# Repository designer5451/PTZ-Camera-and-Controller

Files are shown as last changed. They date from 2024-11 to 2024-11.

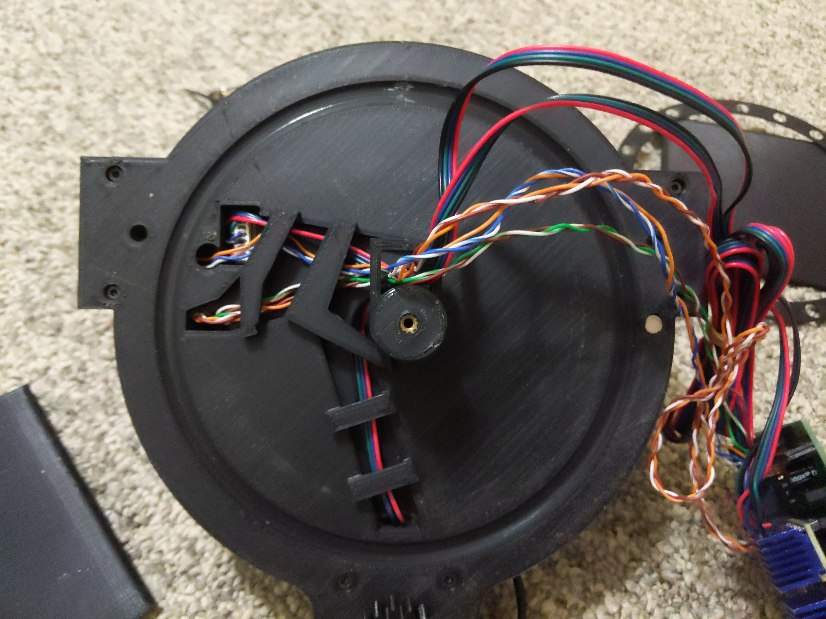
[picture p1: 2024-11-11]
Pictures/22.jpg

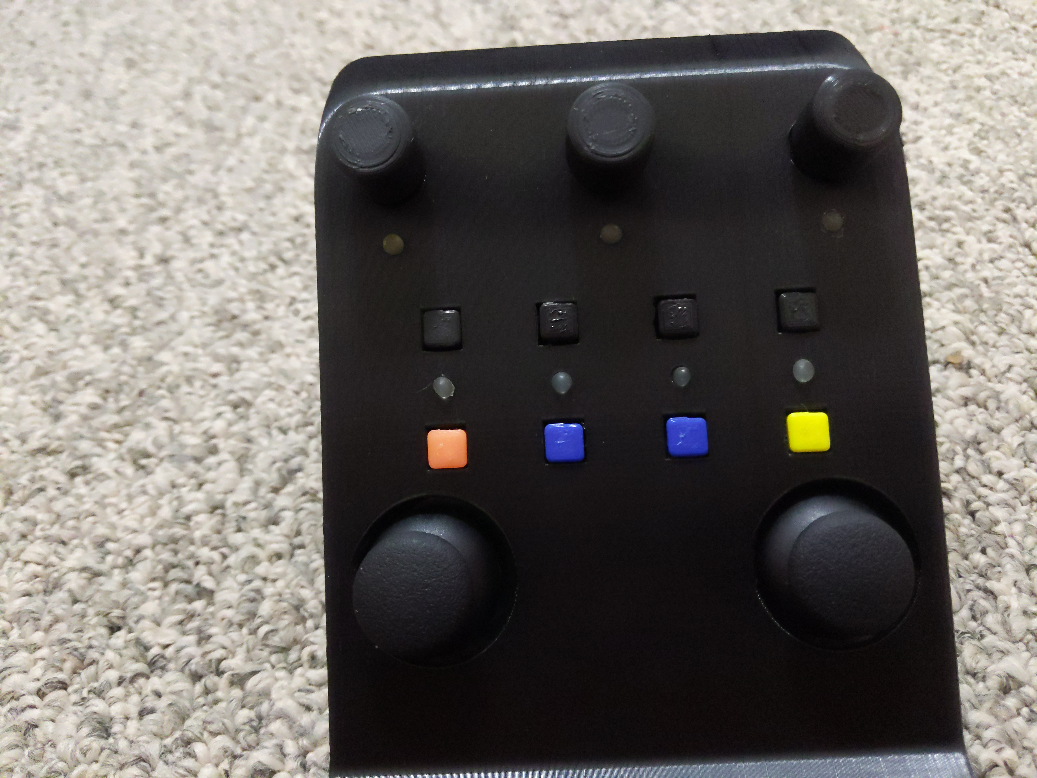
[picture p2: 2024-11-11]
Pictures/14.jpg

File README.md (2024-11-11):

This PTZ camera head uses two ESP32 microcontrollers connected via Ethernet on a standard network, communicating over a TCP connection. The controller acts as the client, while the camera head serves as the server. A PS4 controller connects to the control module via Bluetooth. The PTZ head can pan and tilt the camera and control zoom through a standard 2.5mm LANC interface.

Designed specifically for the Canon Vixia HF G30 camcorder, the PTZ head includes a servo to rotate the camera’s custom control knob. Although optimized for the Canon HF G30, it can work with other cameras that fit within its dimensions and support a standard LANC jack. However, only the Canon HF G30 can utilize the servo control for the custom knob.

The PTZ head’s PCB includes an optional slot for an extra stepper motor, which can be configured to adjust the camera lens manually if you know how to edit Fusion 360 files and the ESP32 program. The controller board program requires updates with the PTZ camera head's IP address and the PS4 controller’s Bluetooth MAC address at the beginning of the program.

To produce the two PCBs, I used JLCPCB, designing the boards in KiCad 8.0. I've attached the KiCad document, Gerber files, and a schematic screenshot. I soldered the components with a "PINECIL – Smart Mini Portable Soldering Iron (Version 2)" from [Pine64](https://pine64.com/product/pinecil-smart-mini-portable-soldering-iron/). The 3D-printed parts were designed in Fusion 360, and I’ve included the Fusion archive file along with all parts as STL files. I printed all of the 3d parts in PLA except for the to drive gears and the gear on the end of the servo which I printed in TPU.

To cushion the base of the controller, I used a hot glue gun to apply small drops, creating soft pads. I also added small glue balls  that I pushed into the controller's light holes to help diffuse the light.

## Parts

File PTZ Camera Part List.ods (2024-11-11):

PTZ
Item | Link to Item (maynot work anymore) | Estimated Price | Quantity | Total Estimated Price | Notes
USR-ES1 W5500 Ethernet Sheild | https://www.aliexpress.us/item/3256804674673261.html | $3.19 | 2 | $6.38
5 pack EC11 encoders 15 mm Half Shaft | https://www.aliexpress.us/item/2251832789732148.html | $2.86 | 1 | $2.86
5.5mm by 2.1mm Power Female Jack | https://www.aliexpress.us/item/2255799848026214.html | $1.35 | 1 | $1.35
Nema 17 42x42x22 Stepper Motor With Dupont Connector | https://www.aliexpress.us/item/3256806667671852.html | $6.07 | 2 | $12.14
10 pack 3144 Hall Effect Sensor | https://www.aliexpress.us/item/3256805950606647.html | $1.26 | 1 | $1.26
50 pack 3.3v-W3 Zener Diode Sod-323 | https://www.aliexpress.us/item/3256806999141284.html | $0.89 | 1 | $0.89
20 Pack 6mm x 2mm Neodymium Magnet | https://www.aliexpress.us/item/3256806180733507.html | $1.32 | 1 | $1.32
3A 5V Buck Converter 12mm by 17mm | https://www.aliexpress.us/item/3256806299955878.html | $0.93 | 1 | $0.93
100 pack 4.7k Resisotrs SMD | https://www.aliexpress.us/item/2251832660828415.html | $1.41 | 1 | $1.41
100 pack 5.6k Resisotrs SMD | https://www.aliexpress.us/item/2251832660828415.html | $1.02 | 1 | $1.02
100 pack 10k Resisotrs SMD | https://www.aliexpress.us/item/2251832660828415.html | $1.02 | 1 | $1.02
100 pack MMBT30094 LAM SOT-23 SMD Transistor | https://www.aliexpress.us/item/3256806841505571.html | $0.83 | 1 | $0.83
3A 12V DC Power Supply 5.5mm by 2.1mm | https://www.aliexpress.us/item/3256806788215801.html | $3.37 | 1 | $3.37
25V 100UF 6mmX7mm Aluminum electrolytic capacitor | https://www.aliexpress.us/item/3256806593044514.html | $1.45 | 1 | $1.45
TMC2209 Stepper Motor Driver | https://www.aliexpress.us/item/3256804676423170.html | $2.95 | 3 | $8.85
¼” Tripod Screw | https://www.aliexpress.us/item/3256806761503223.html | $1.36 | 1 | $1.36
38 Pin USB-C ESP32 Development Board | https://www.aliexpress.us/item/3256806034074322.html | $3.68 | 2 | $7.36
10PCS Single Row Pin Female Header Socket Pitch 2.54mm 40pin | https://www.aliexpress.us/item/2255801012106911.html | $1.82 | 1 | $1.82
10PCS Single Row Pin male Header Socket Pitch 2.54mm 40pin | https://www.aliexpress.us/item/2251832786866410.html | $2.82 | 2 | $5.64
7mm Diameter/50pcs Steel Ball | https://www.aliexpress.us/item/3256807294706153.html | $3.04 | 1 | $3.04
2 Pack PS4 Hall Effect Joystick | https://www.aliexpress.us/item/3256807040936656.html | $2.91 | 2 | $5.82 | The Yellow snap one sensor on the joysticks did not work so I had to buy twice as many as I needed and only used the black Sensors
MG995 360 degree servo | https://www.aliexpress.us/item/3256806668097478.html | $3.99 | 1 | $3.99
Bearings insides 8 mm outside 22 mm 8 Pack | https://www.aliexpress.us/item/3256807670760874.htm | $3.09 | 1 | $3.09
SMD Switches 5.2*5.2*1.5mm | https://www.aliexpress.us/item/3256804125700359.html | $0.97 | 1 | $0.97
5050 SK6812 20 Pack SMD Leds | https://www.aliexpress.us/item/3256806129701481.html | $5.00 | 1 | $5.00
SMD 10 NF capacitors 100 pack | https://www.aliexpress.us/item/2251832706484294.html | $1.81 | 1 | $1.81
M1.6 M2 M2.5 M3 M4 M5 Black Grade 12.9 Steel Hexagon Hex Socket Cap Head Screw | https://www.aliexpress.us/item/3256805018016735.html | $10.16 | 1 | $10.16
M2 M2.5 M3 M4 M5 M6 Heat Set Threaded Insert Brass Nut Hot Melt Knurled Inserts | https://www.aliexpress.us/item/3256805041162703.html | $2.79 | 1 | $2.79
Thumbstick Mushroom Cap For Sony PlayStation 4 PS4 Controlle 10 pack | https://www.aliexpress.us/item/3256807619216954.html | $1.84 | 1 | $1.84
2.5mm 3Pole Male 9 inch Cable | https://www.aliexpress.us/item/3256805153533109.html | $2.10 | 1 | $2.10
18 gauge wire for hall sensors and extending servo cord | https://www.aliexpress.us/item/3256806969799753.html | $4.43 | 1 | $4.43 | I used the wires in side ethernet riser cable
3X9X0.8 Washer 3 Needed | https://www.aliexpress.us/item/3256805615609918.html | $1.40 | 1 | $1.40
 |  |  |  | $107.70

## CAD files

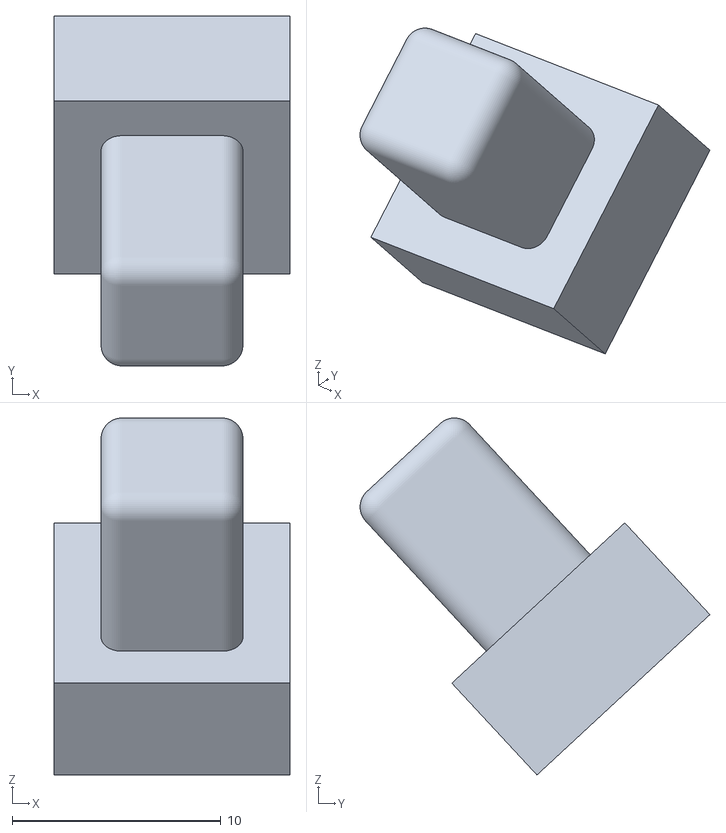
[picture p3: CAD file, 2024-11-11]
3D Files/PTZ_Camera_Controler/Button 1.stl
11.3 x 16.8 x 17.1

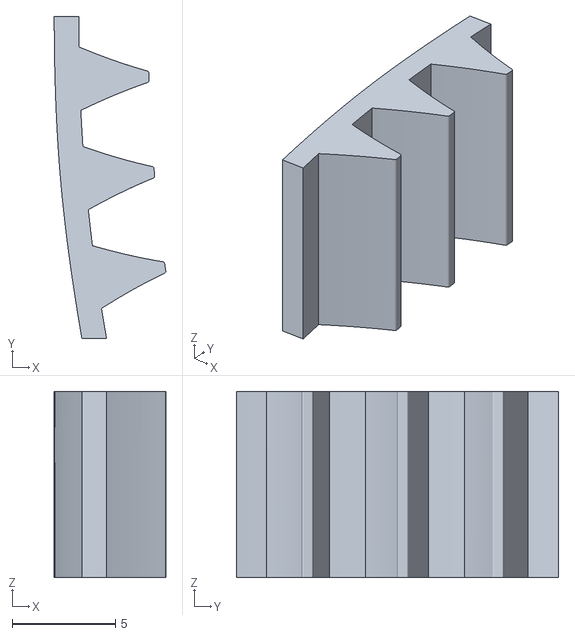
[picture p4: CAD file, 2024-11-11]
3D Files/PTZ_Camera_Head/Right Stopper.stl
5.40 x 15.6 x 9.00

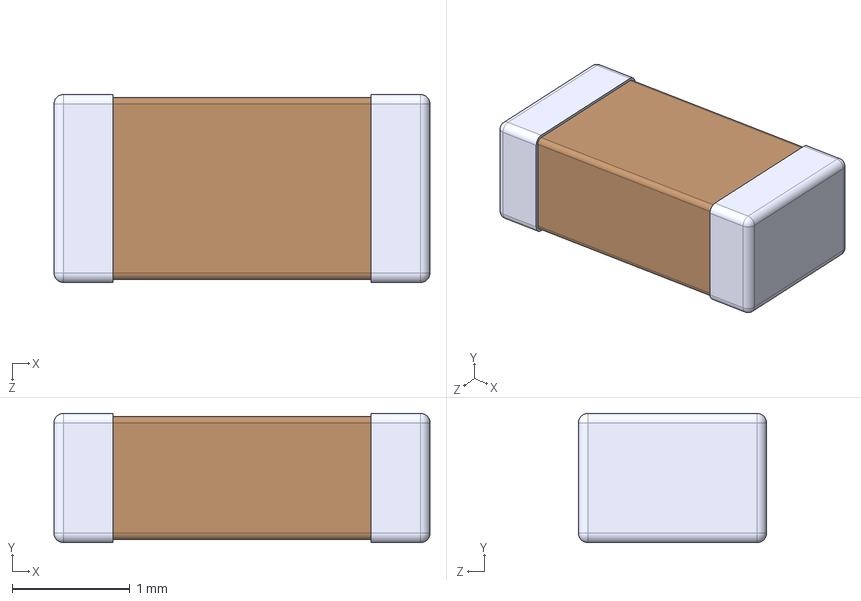
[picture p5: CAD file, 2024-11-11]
PCB Boards/PTZ_Camera_Controler V1.2/Custom Footprints/C1206C105K5RACTU_Capacitor/C1206C105K5RACTU.step
3.20 x 1.10 x 1.60 mm

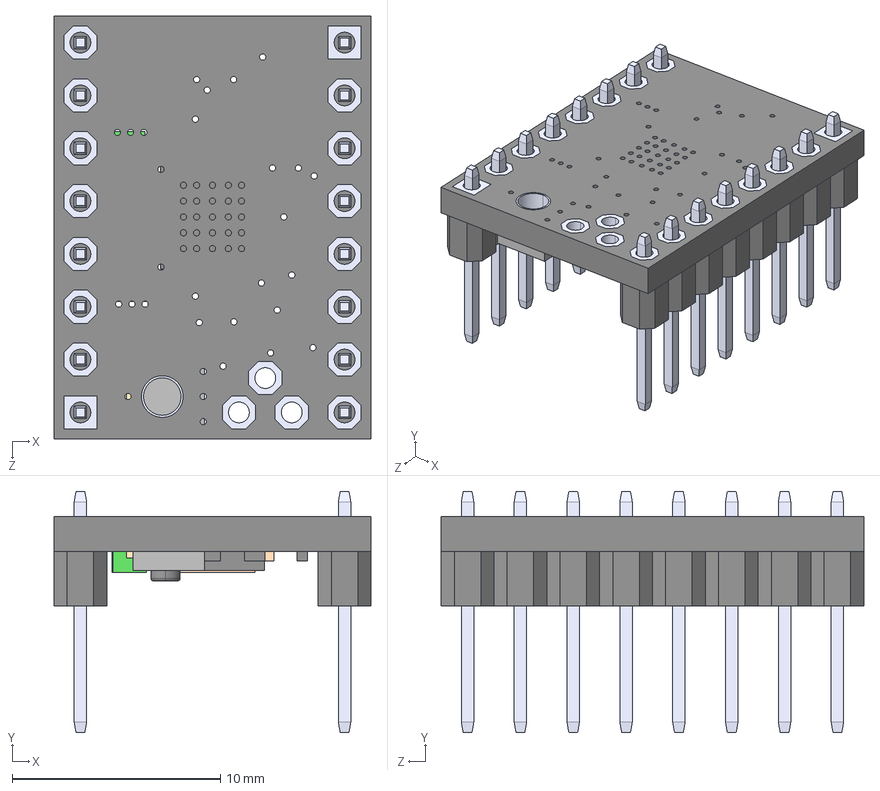
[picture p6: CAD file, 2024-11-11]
PCB Boards/PTZ_Camera_Controler V1.2/Custom Footprints/TMC2209_SILENTSTEPSTICK/TMC2209_SILENTSTEPSTICK.step
15.2 x 11.6 x 20.3 mm

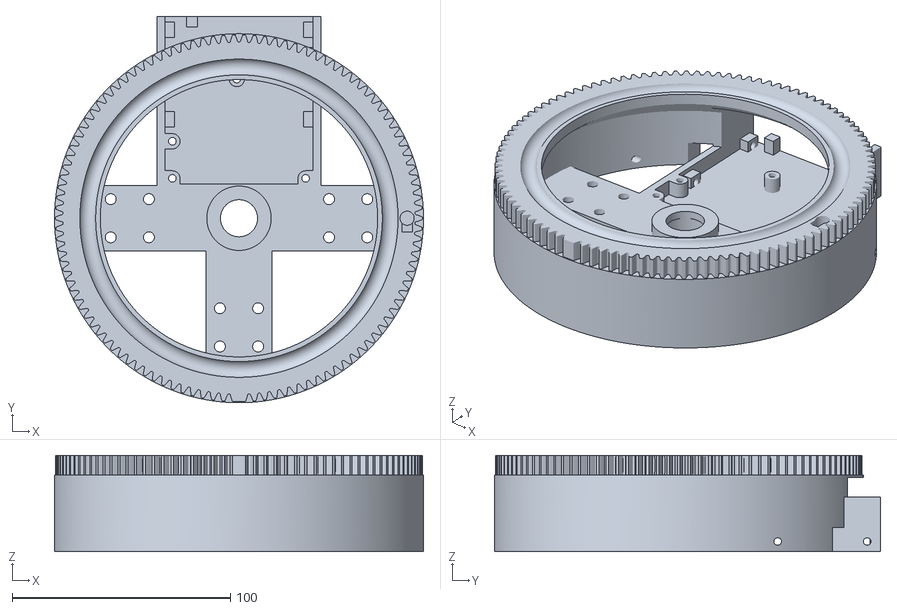
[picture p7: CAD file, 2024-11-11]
3D Files/PTZ_Camera_Head/Base.stl
169.0 x 177.0 x 44.0

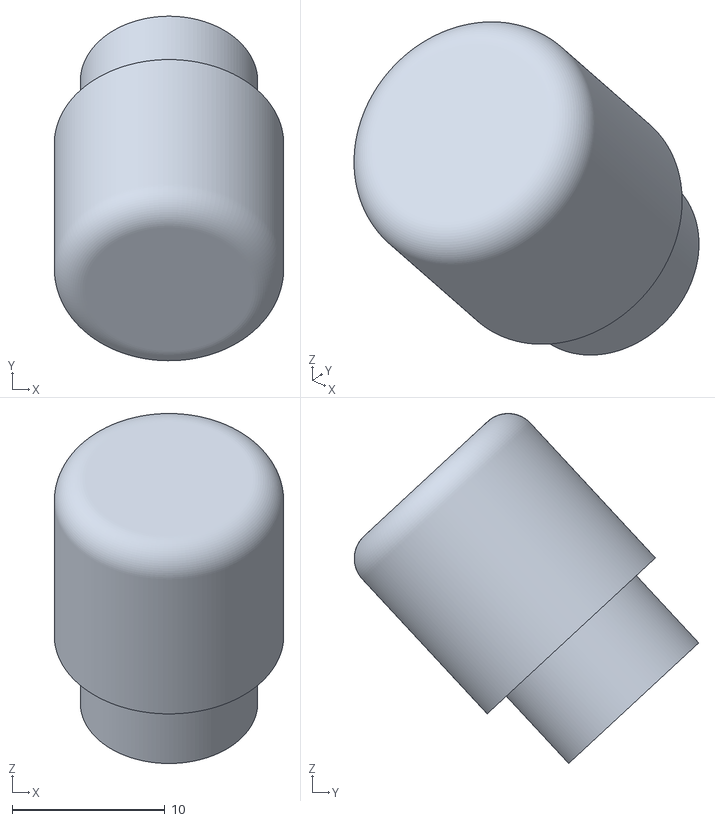
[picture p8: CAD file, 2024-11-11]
3D Files/PTZ_Camera_Controler/Knob 2.stl
15.0 x 22.5 x 22.9

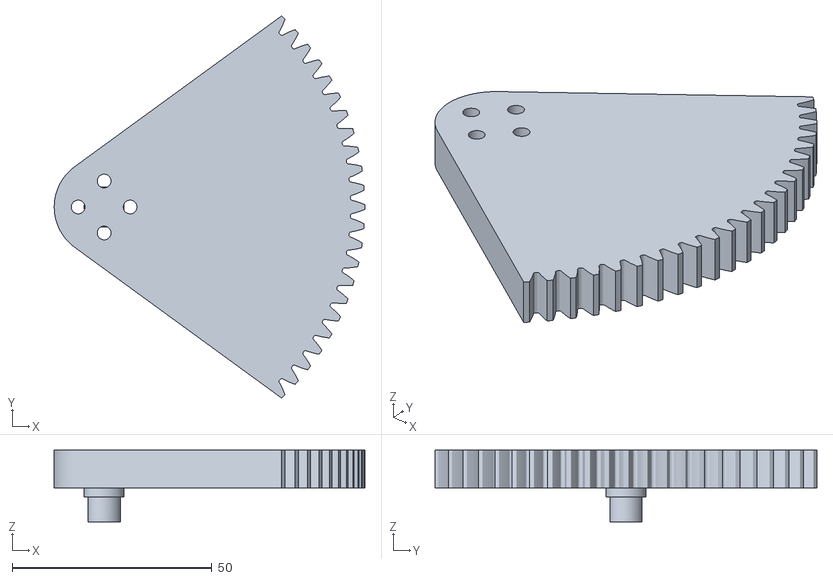
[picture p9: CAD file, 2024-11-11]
3D Files/PTZ_Camera_Head/Spur Gear (85 teeth).stl
77.7 x 95.6 x 18.0

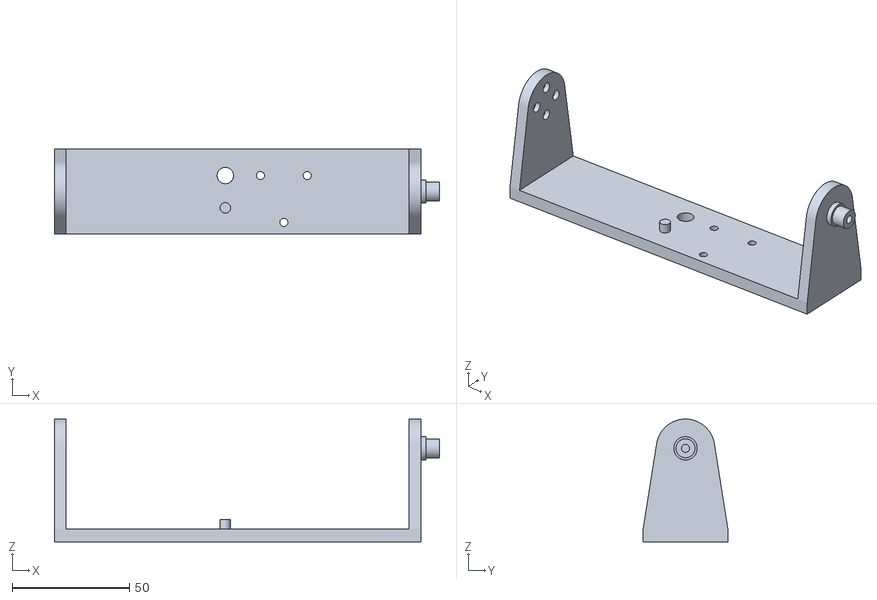
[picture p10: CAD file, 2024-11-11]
3D Files/PTZ_Camera_Head/Camera Holder.stl
164.5 x 36.3 x 52.5

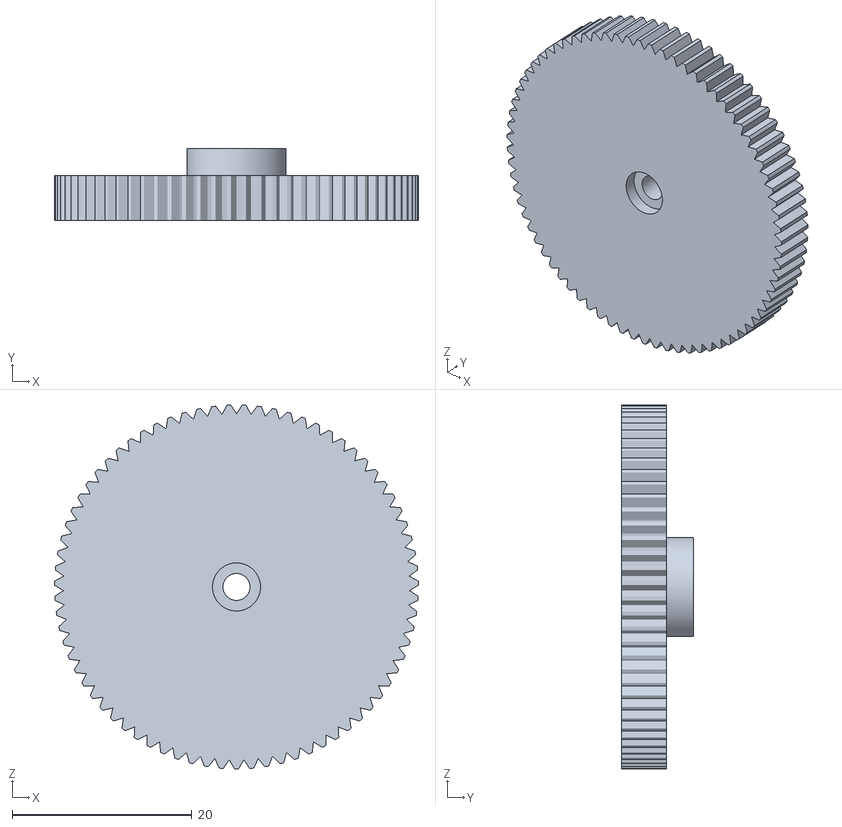
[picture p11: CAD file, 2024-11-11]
3D Files/PTZ_Camera_Head/Wheel for Servo.stl
40.5 x 8.00 x 40.5

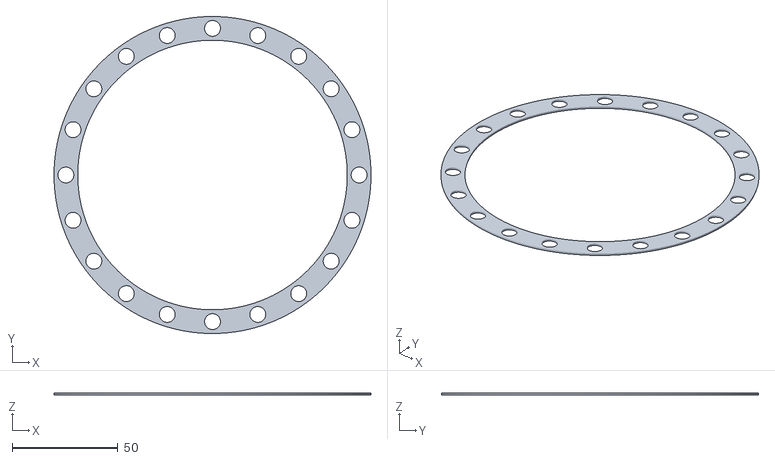
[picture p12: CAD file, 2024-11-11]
3D Files/PTZ_Camera_Head/Bearing Spacer.stl
149.7 x 149.7 x 1.00

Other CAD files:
3D Files/PTZ_Camera_Head/Left Stopper.stl
3D Files/PTZ_Camera_Controler/Back Bottom Plate.stl
3D Files/PTZ_Camera_Controler/Back Plate.stl
3D Files/PTZ_Camera_Controler/Base.stl
3D Files/PTZ_Camera_Controler/Controler+for+PTZ+Camera.f3d
3D Files/PTZ_Camera_Head/Cable Holder.stl
3D Files/PTZ_Camera_Head/Left Side Arm.stl
3D Files/PTZ_Camera_Head/Right Side Arm.stl
3D Files/PTZ_Camera_Head/Servo Holder.stl
3D Files/PTZ_Camera_Head/Spur Gear (14 teeth) (1).stl
3D Files/PTZ_Camera_Head/Spur Gear (14 teeth).stl
3D Files/PTZ_Camera_Head/Top.stl
3D Files/PTZ_Camera_Head/Wall Mount.stl

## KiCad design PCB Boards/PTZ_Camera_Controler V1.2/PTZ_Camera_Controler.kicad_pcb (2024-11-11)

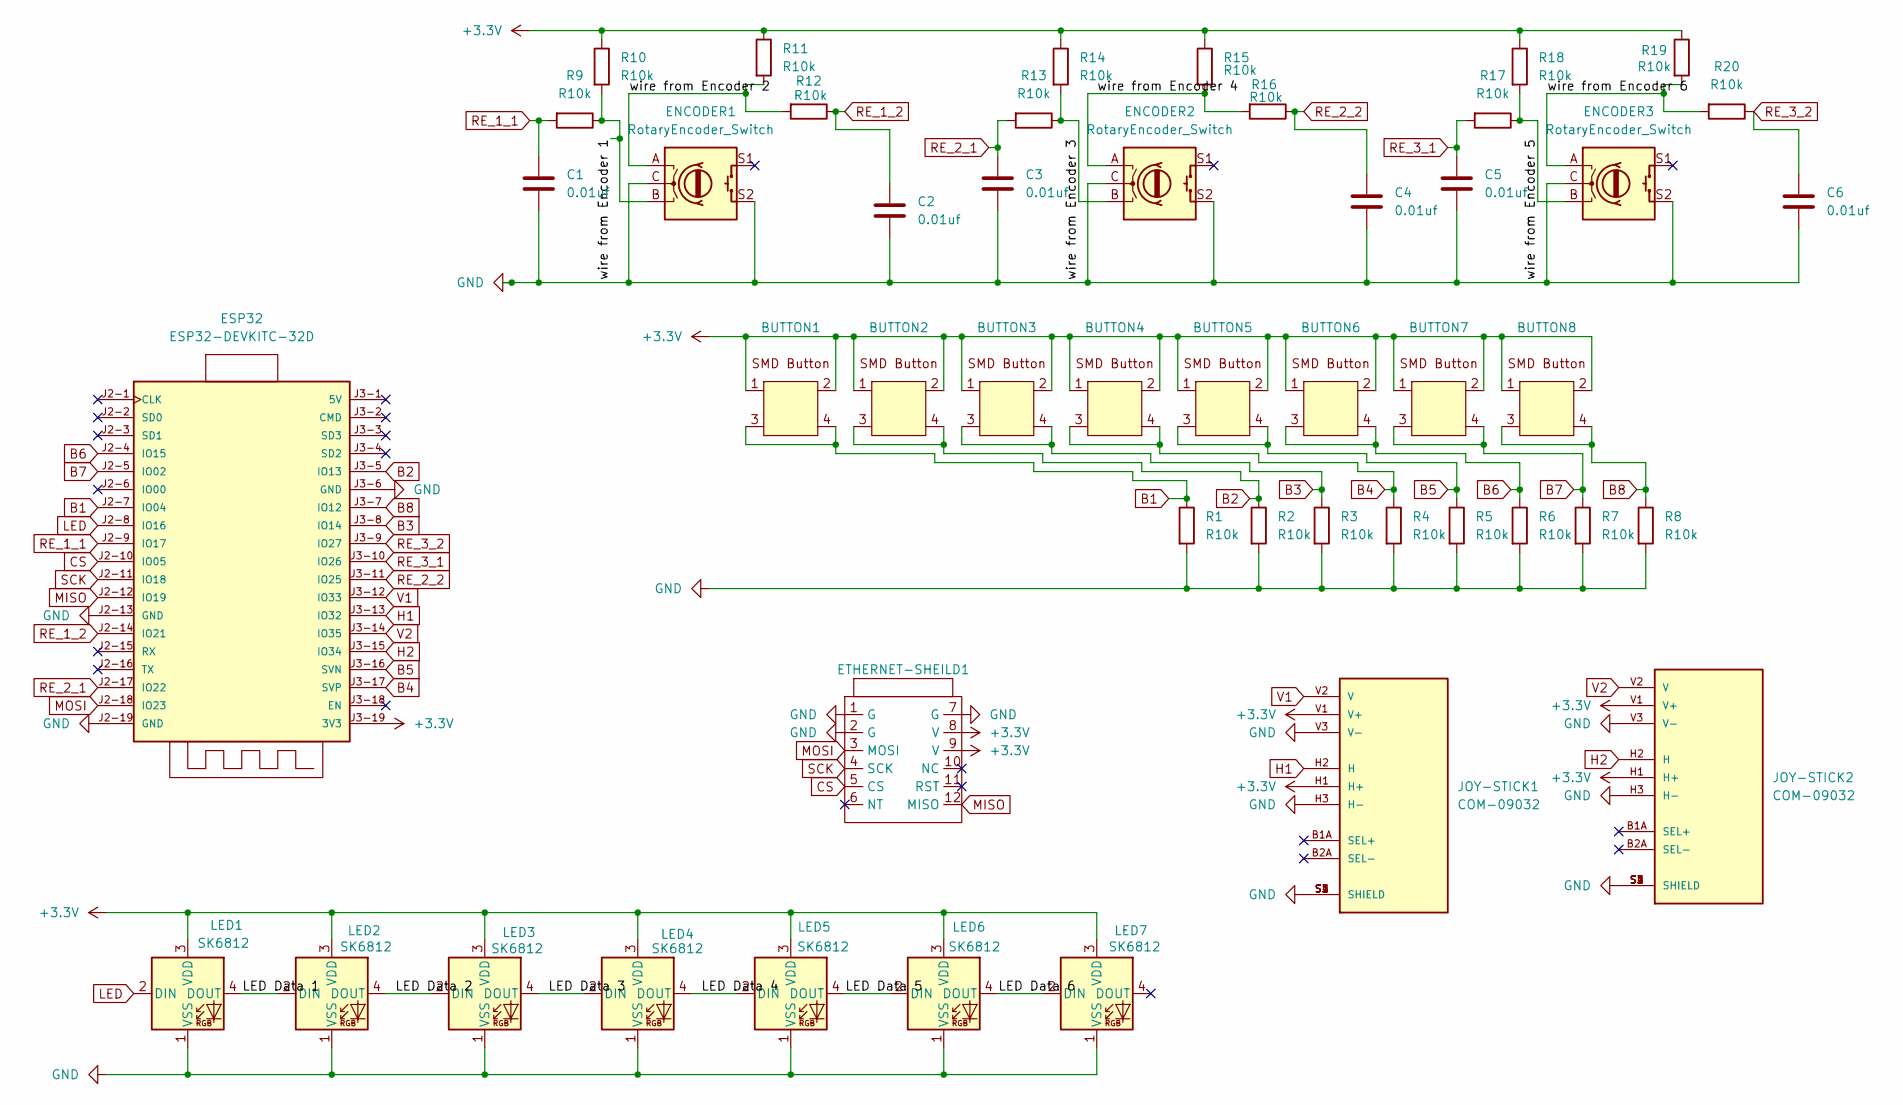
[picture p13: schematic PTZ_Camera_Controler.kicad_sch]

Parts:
BUTTON1, BUTTON2, BUTTON3, BUTTON4, BUTTON5, BUTTON6, BUTTON7, BUTTON8: TWS4417-250AT
C1, C2, C3, C4, C5, C6: 0.01uf; C_1206_3216Metric_Pad1.33x1.80mm_HandSolder
ENCODER1, ENCODER2, ENCODER3: RotaryEncoder_Switch; RotaryEncoder_Alps_EC11E-Switch_Vertical_H20mm
ESP32: ESP32-DEVKITC-32D; MODULE_ESP32-DEVKITC-32D; PARTREV V4
ETHERNET-SHEILD1: W5500_mini_ethernet_sheild
JOY-STICK1, JOY-STICK2: COM-09032; PARTREV N/A
LED1, LED2, LED3, LED4, LED5, LED6, LED7: SK6812; LED_SK6812_PLCC4_5.0x5.0mm_P3.2mm
R1, R2, R3, R4, R5, R6, R7, R8, R9, R10, R11, R12, R13, R14, R15, R16, R17, R18, R19, R20: R10k; R_1206_3216Metric

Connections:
+3.3V: BUTTON1.1, BUTTON1.2, BUTTON2.1, BUTTON2.2, BUTTON3.1, BUTTON3.2, BUTTON4.1, BUTTON4.2, BUTTON5.1, BUTTON5.2, BUTTON6.1, BUTTON6.2, BUTTON7.1, BUTTON7.2, BUTTON8.1, BUTTON8.2, ESP32.J3-19 (3V3), ETHERNET-SHEILD1.8 (V), ETHERNET-SHEILD1.9 (V), JOY-STICK1.H1 (H+), JOY-STICK1.V1 (V+), JOY-STICK2.H1 (H+), JOY-STICK2.V1 (V+), LED1.3 (VDD), LED2.3 (VDD), LED3.3 (VDD), LED4.3 (VDD), LED5.3 (VDD), LED6.3 (VDD), LED7.3 (VDD), R10.1, R11.1, R14.1, R15.1, R18.1, R19.1
/LED Data 1: LED1.4 (DOUT), LED2.2 (DIN)
/LED Data 2: LED2.4 (DOUT), LED3.2 (DIN)
/LED Data 3: LED3.4 (DOUT), LED4.2 (DIN)
/LED Data 4: LED4.4 (DOUT), LED5.2 (DIN)
/LED Data 5: LED5.4 (DOUT), LED6.2 (DIN)
/LED Data 6: LED6.4 (DOUT), LED7.2 (DIN)
/wire from Encoder 1: ENCODER1.B, R9.1, R10.2
/wire from Encoder 2: ENCODER1.A, R11.2, R12.2
/wire from Encoder 3: ENCODER2.B, R13.1, R14.2
/wire from Encoder 4: ENCODER2.A, R15.2, R16.2
/wire from Encoder 5: ENCODER3.B, R17.1, R18.2
/wire from Encoder 6: ENCODER3.A, R19.2, R20.2
B1: BUTTON1.3, BUTTON1.4, ESP32.J2-7 (IO04), R1.1
B2: BUTTON2.3, BUTTON2.4, ESP32.J3-5 (IO13), R2.1
B3: BUTTON3.3, BUTTON3.4, ESP32.J3-8 (IO14), R3.1
B4: BUTTON4.3, BUTTON4.4, ESP32.J3-17 (SVP), R4.1
B5: BUTTON5.3, BUTTON5.4, ESP32.J3-16 (SVN), R5.1
B6: BUTTON6.3, BUTTON6.4, ESP32.J2-4 (IO15), R6.1
B7: BUTTON7.3, BUTTON7.4, ESP32.J2-5 (IO02), R7.1
B8: BUTTON8.3, BUTTON8.4, ESP32.J3-7 (IO12), R8.1
CS: ESP32.J2-10 (IO05), ETHERNET-SHEILD1.5 (CS)
GND: C1.2, C2.2, C3.2, C4.2, C5.2, C6.2, ENCODER1.C, ENCODER1.S2, ENCODER2.C, ENCODER2.S2, ENCODER3.C, ENCODER3.S2, ESP32.J2-13 (GND), ESP32.J2-19 (GND), ESP32.J3-6 (GND), ETHERNET-SHEILD1.1 (G), ETHERNET-SHEILD1.2 (G), ETHERNET-SHEILD1.7 (G), JOY-STICK1.H3 (H-), JOY-STICK1.S1 (SHIELD), JOY-STICK1.S2 (SHIELD), JOY-STICK1.S3 (SHIELD), JOY-STICK1.S4 (SHIELD), JOY-STICK1.V3 (V-), JOY-STICK2.H3 (H-), JOY-STICK2.S1 (SHIELD), JOY-STICK2.S2 (SHIELD), JOY-STICK2.S3 (SHIELD), JOY-STICK2.S4 (SHIELD), JOY-STICK2.V3 (V-), LED1.1 (VSS), LED2.1 (VSS), LED3.1 (VSS), LED4.1 (VSS), LED5.1 (VSS), LED6.1 (VSS), LED7.1 (VSS), R1.2, R2.2, R3.2, R4.2, R5.2, R6.2, R7.2, R8.2
H1: ESP32.J3-13 (IO32), JOY-STICK1.H2 (H)
H2: ESP32.J3-15 (IO34), JOY-STICK2.H2 (H)
LED: ESP32.J2-8 (IO16), LED1.2 (DIN)
MISO: ESP32.J2-12 (IO19), ETHERNET-SHEILD1.12 (MISO)
MOSI: ESP32.J2-18 (IO23), ETHERNET-SHEILD1.3 (MOSI)
RE_1_1: C1.1, ESP32.J2-9 (IO17), R9.2
RE_1_2: C2.1, ESP32.J2-14 (IO21), R12.1
RE_2_1: C3.1, ESP32.J2-17 (IO22), R13.2
RE_2_2: C4.1, ESP32.J3-11 (IO25), R16.1
RE_3_1: C5.1, ESP32.J3-10 (IO26), R17.2
RE_3_2: C6.1, ESP32.J3-9 (IO27), R20.1
SCK: ESP32.J2-11 (IO18), ETHERNET-SHEILD1.4 (SCK)
V1: ESP32.J3-12 (IO33), JOY-STICK1.V2 (V)
V2: ESP32.J3-14 (IO35), JOY-STICK2.V2 (V)

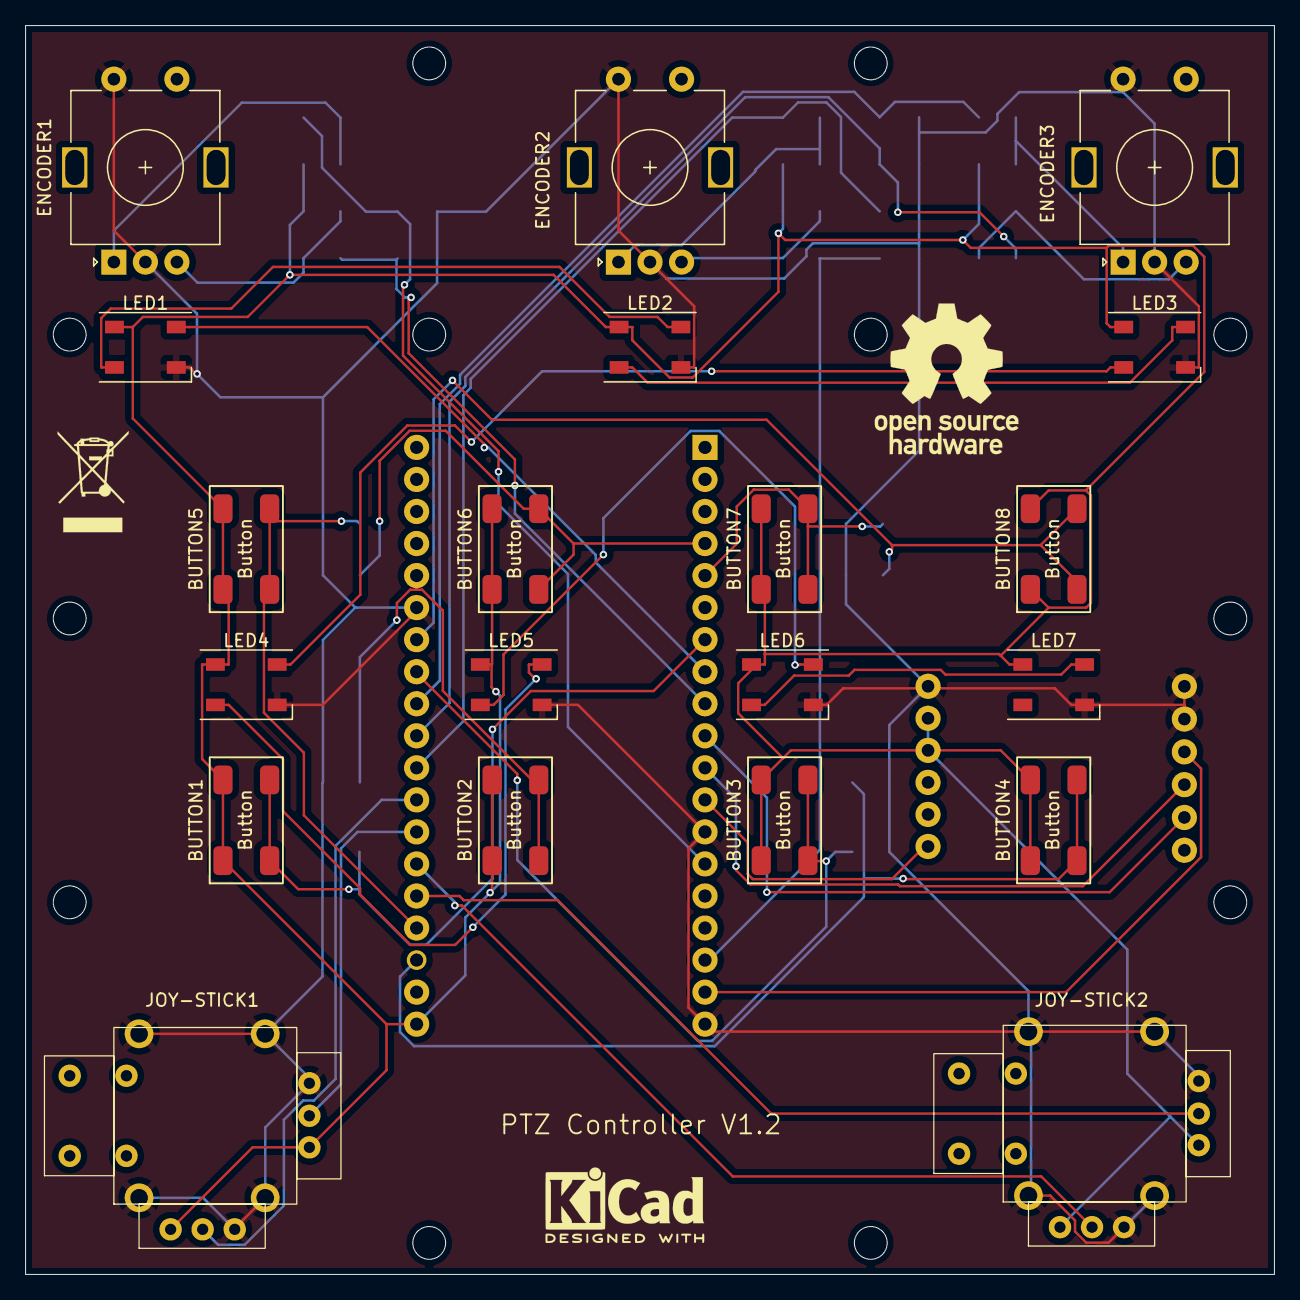
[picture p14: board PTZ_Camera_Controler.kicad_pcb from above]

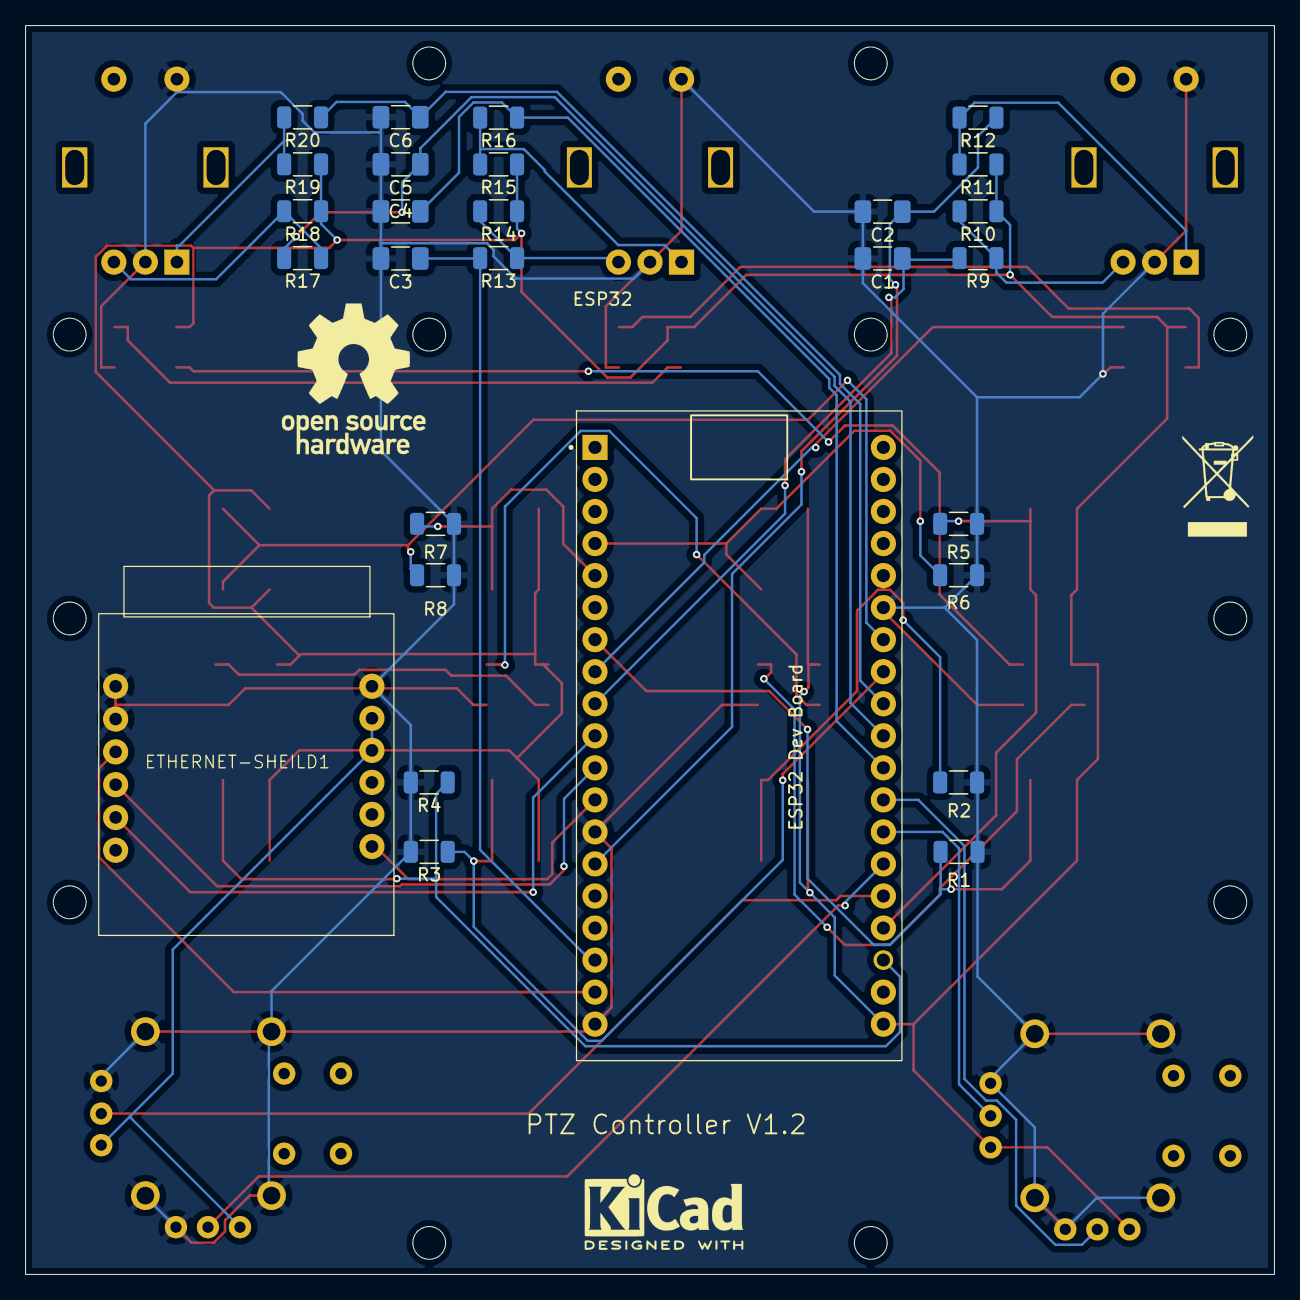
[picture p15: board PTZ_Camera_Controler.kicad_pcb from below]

Board: 2 copper layers, 99.0 x 99.0 mm, 54 parts (31 on the bottom side), 37 nets.

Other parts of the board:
REF1, REF2: KiCad-Logo2_5mm_SilkScreen
REF3, REF4: OSHW-Logo_11.4x12mm_SilkScreen
REF5, REF6: WEEE-Logo_5.6x8mm_SilkScreen

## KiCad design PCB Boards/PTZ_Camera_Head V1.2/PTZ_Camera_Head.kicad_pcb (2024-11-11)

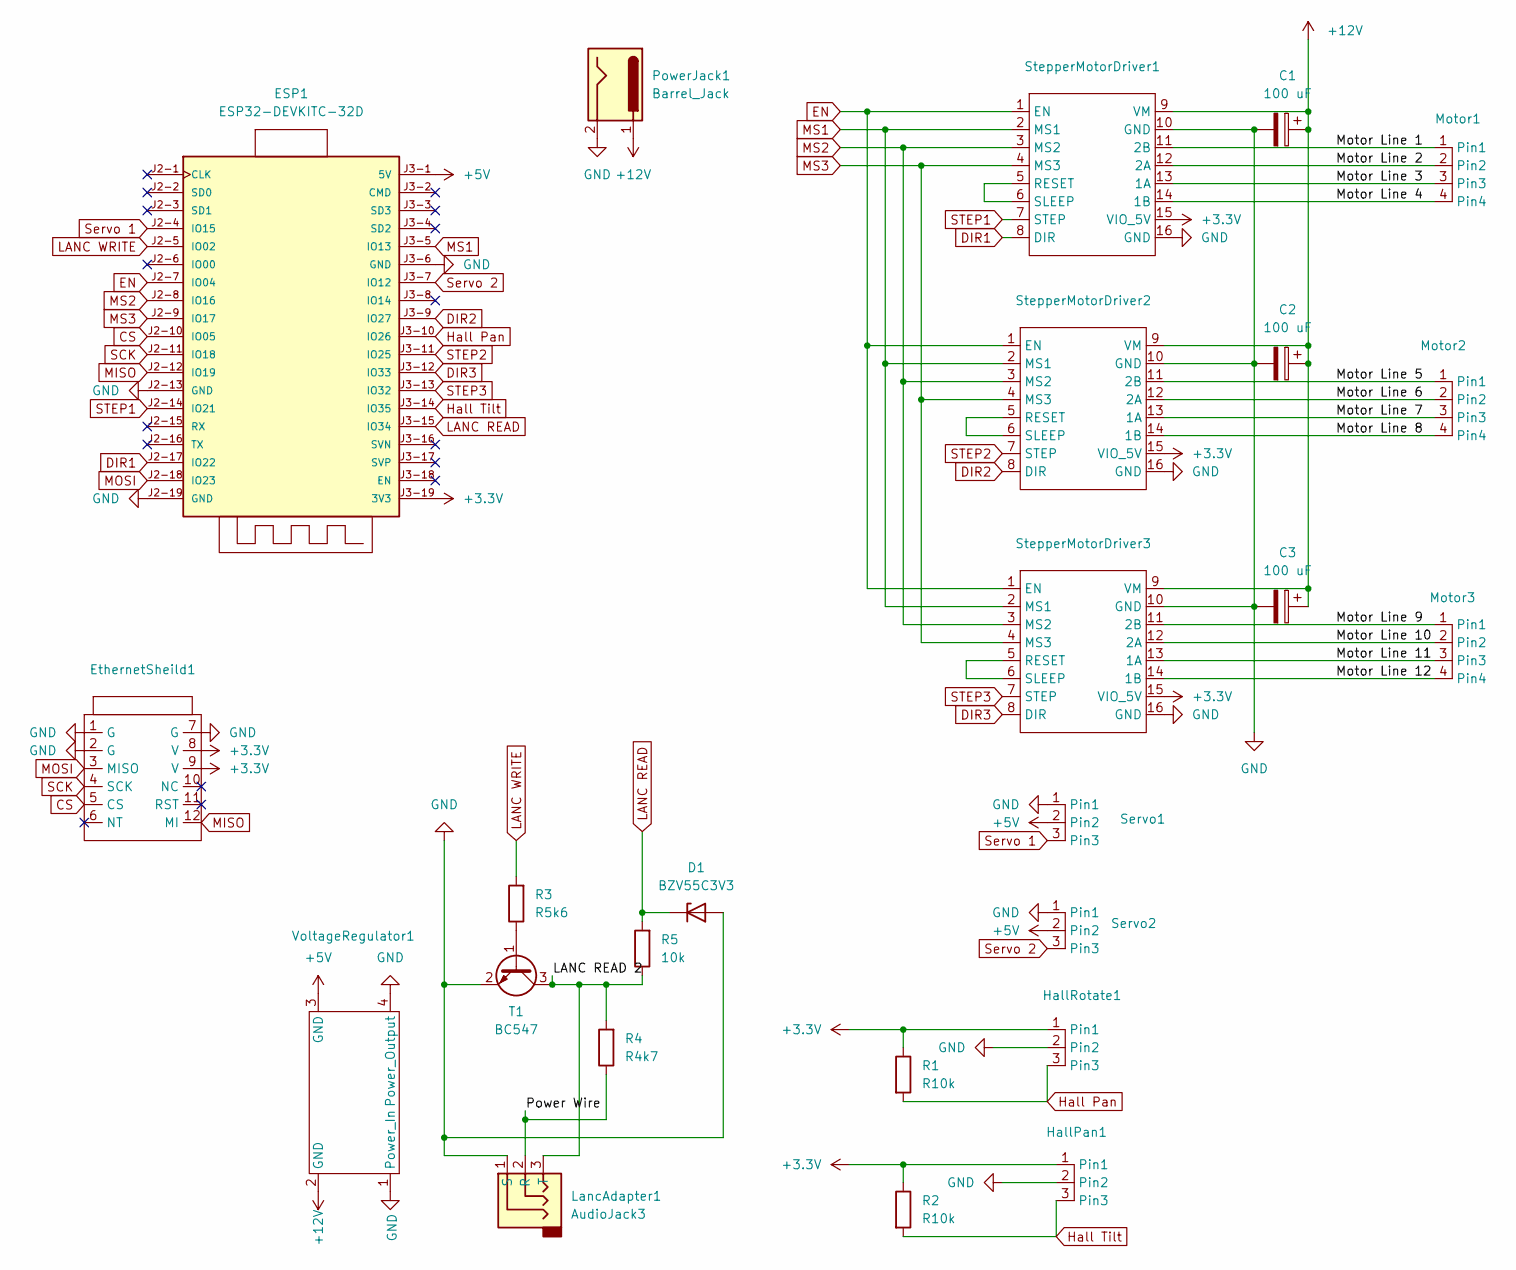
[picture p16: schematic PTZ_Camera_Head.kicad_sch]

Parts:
C1, C2, C3: 100 uF; CP_Radial_D5.0mm_P2.50mm
D1: BZV55C3V3; D_MiniMELF
ESP1: ESP32-DEVKITC-32D; MODULE_ESP32-DEVKITC-32D; PARTREV V4
EthernetSheild1: W5500_mini_ethernet_sheild
HallPan1: PinHeader_1x03_P2.54mm_Vertical
HallRotate1: PinHeader_1x03_P2.54mm_Vertical
LancAdapter1: AudioJack3; PinHeader_1x03_P2.54mm_Vertical
Motor1, Motor2, Motor3: PinHeader_1x04_P2.54mm_Vertical
PowerJack1: Barrel_Jack; BarrelJack_Wuerth_6941xx301002
R1, R2: R10k; R_1206_3216Metric
R3: R5k6; R_1206_3216Metric
R4: R4k7; R_1206_3216Metric
R5: 10k; R_1206_3216Metric
Servo1, Servo2: PinHeader_1x03_P2.54mm_Vertical
StepperMotorDriver1, StepperMotorDriver2, StepperMotorDriver3: MODULE_TMC2209_SILENTSTEPSTICK
T1: BC547; SOT-23_Handsoldering
VoltageRegulator1: voltage_regulator_17_12mm

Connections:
+3.3V: ESP1.J3-19 (3V3), EthernetSheild1.8 (V), EthernetSheild1.9 (V), HallPan1.1 (Pin1), HallRotate1.1 (Pin1), R1.1, R2.1, StepperMotorDriver1.15 (VIO_5V), StepperMotorDriver2.15 (VIO_5V), StepperMotorDriver3.15 (VIO_5V)
+5V: ESP1.J3-1 (5V), Servo1.2 (Pin2), Servo2.2 (Pin2), VoltageRegulator1.3 (GND)
+12V: C1.1, C2.1, C3.1, PowerJack1.1, StepperMotorDriver1.9 (VM), StepperMotorDriver2.9 (VM), StepperMotorDriver3.9 (VM), VoltageRegulator1.2 (GND)
/LANC READ 2: LancAdapter1.3 (T), R4.2, R5.1, T1.3 (C)
/Motor Line 1: Motor1.1 (Pin1), StepperMotorDriver1.11 (2B)
/Motor Line 2: Motor1.2 (Pin2), StepperMotorDriver1.12 (2A)
/Motor Line 3: Motor1.3 (Pin3), StepperMotorDriver1.13 (1A)
/Motor Line 4: Motor1.4 (Pin4), StepperMotorDriver1.14 (1B)
/Motor Line 5: Motor2.1 (Pin1), StepperMotorDriver2.11 (2B)
/Motor Line 6: Motor2.2 (Pin2), StepperMotorDriver2.12 (2A)
/Motor Line 7: Motor2.3 (Pin3), StepperMotorDriver2.13 (1A)
/Motor Line 8: Motor2.4 (Pin4), StepperMotorDriver2.14 (1B)
/Motor Line 9: Motor3.1 (Pin1), StepperMotorDriver3.11 (2B)
/Motor Line 10: Motor3.2 (Pin2), StepperMotorDriver3.12 (2A)
/Motor Line 11: Motor3.3 (Pin3), StepperMotorDriver3.13 (1A)
/Motor Line 12: Motor3.4 (Pin4), StepperMotorDriver3.14 (1B)
/Power Wire: LancAdapter1.2 (R), R4.1
CS: ESP1.J2-10 (IO05), EthernetSheild1.5 (CS)
DIR1: ESP1.J2-17 (IO22), StepperMotorDriver1.8 (DIR)
DIR2: ESP1.J3-9 (IO27), StepperMotorDriver2.8 (DIR)
DIR3: ESP1.J3-12 (IO33), StepperMotorDriver3.8 (DIR)
EN: ESP1.J2-7 (IO04), StepperMotorDriver1.1 (EN), StepperMotorDriver2.1 (EN), StepperMotorDriver3.1 (EN)
GND: C1.2, C2.2, C3.2, D1.2 (A), ESP1.J2-13 (GND), ESP1.J2-19 (GND), ESP1.J3-6 (GND), EthernetSheild1.1 (G), EthernetSheild1.2 (G), EthernetSheild1.7 (G), HallPan1.2 (Pin2), HallRotate1.2 (Pin2), LancAdapter1.1 (S), PowerJack1.2, Servo1.1 (Pin1), Servo2.1 (Pin1), StepperMotorDriver1.10 (GND), StepperMotorDriver1.16 (GND), StepperMotorDriver2.10 (GND), StepperMotorDriver2.16 (GND), StepperMotorDriver3.10 (GND), StepperMotorDriver3.16 (GND), T1.2 (E), VoltageRegulator1.1 (Power_In), VoltageRegulator1.4 (Power_Output)
Hall Pan: ESP1.J3-10 (IO26), HallRotate1.3 (Pin3), R1.2
Hall Tilt: ESP1.J3-14 (IO35), HallPan1.3 (Pin3), R2.2
LANC READ: D1.1 (K), ESP1.J3-15 (IO34), R5.2
LANC WRITE: ESP1.J2-5 (IO02), R3.2
MISO: ESP1.J2-12 (IO19), EthernetSheild1.12 (MI)
MOSI: ESP1.J2-18 (IO23), EthernetSheild1.3 (MISO)
MS1: ESP1.J3-5 (IO13), StepperMotorDriver1.2 (MS1), StepperMotorDriver2.2 (MS1), StepperMotorDriver3.2 (MS1)
MS2: ESP1.J2-8 (IO16), StepperMotorDriver1.3 (MS2), StepperMotorDriver2.3 (MS2), StepperMotorDriver3.3 (MS2)
MS3: ESP1.J2-9 (IO17), StepperMotorDriver1.4 (MS3), StepperMotorDriver2.4 (MS3), StepperMotorDriver3.4 (MS3)
unnamed: StepperMotorDriver1.5 (RESET), StepperMotorDriver1.6 (SLEEP)
unnamed: StepperMotorDriver2.5 (RESET), StepperMotorDriver2.6 (SLEEP)
unnamed: StepperMotorDriver3.5 (RESET), StepperMotorDriver3.6 (SLEEP)
unnamed: R3.1, T1.1 (B)
SCK: ESP1.J2-11 (IO18), EthernetSheild1.4 (SCK)
STEP1: ESP1.J2-14 (IO21), StepperMotorDriver1.7 (STEP)
STEP2: ESP1.J3-11 (IO25), StepperMotorDriver2.7 (STEP)
STEP3: ESP1.J3-13 (IO32), StepperMotorDriver3.7 (STEP)
Servo 1: ESP1.J2-4 (IO15), Servo1.3 (Pin3)
Servo 2: ESP1.J3-7 (IO12), Servo2.3 (Pin3)

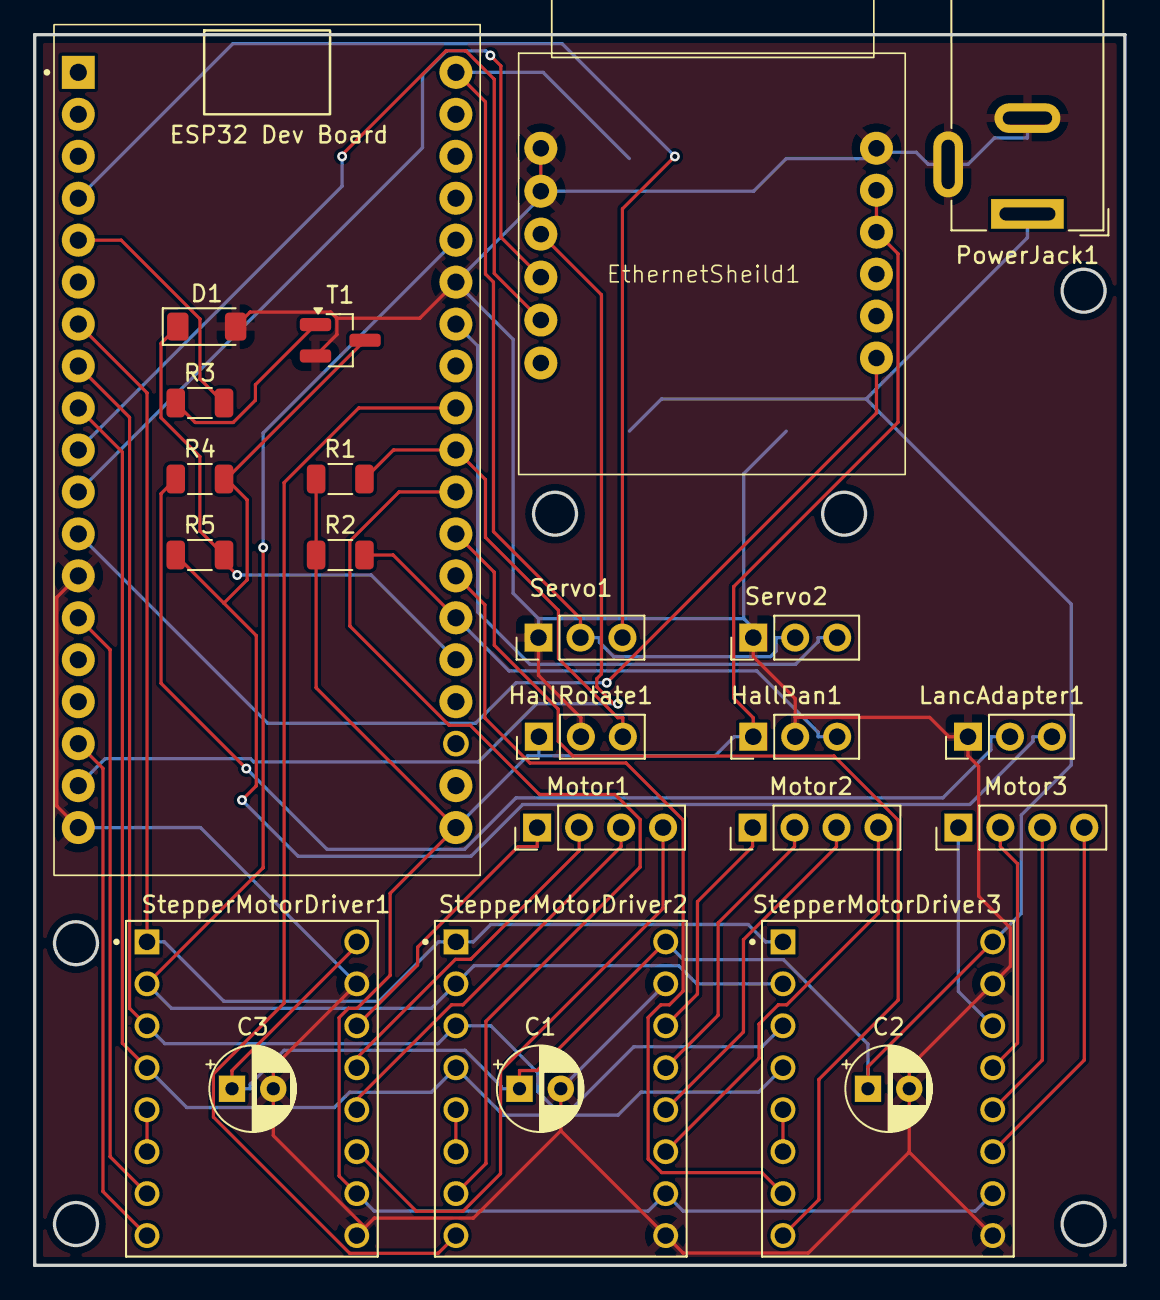
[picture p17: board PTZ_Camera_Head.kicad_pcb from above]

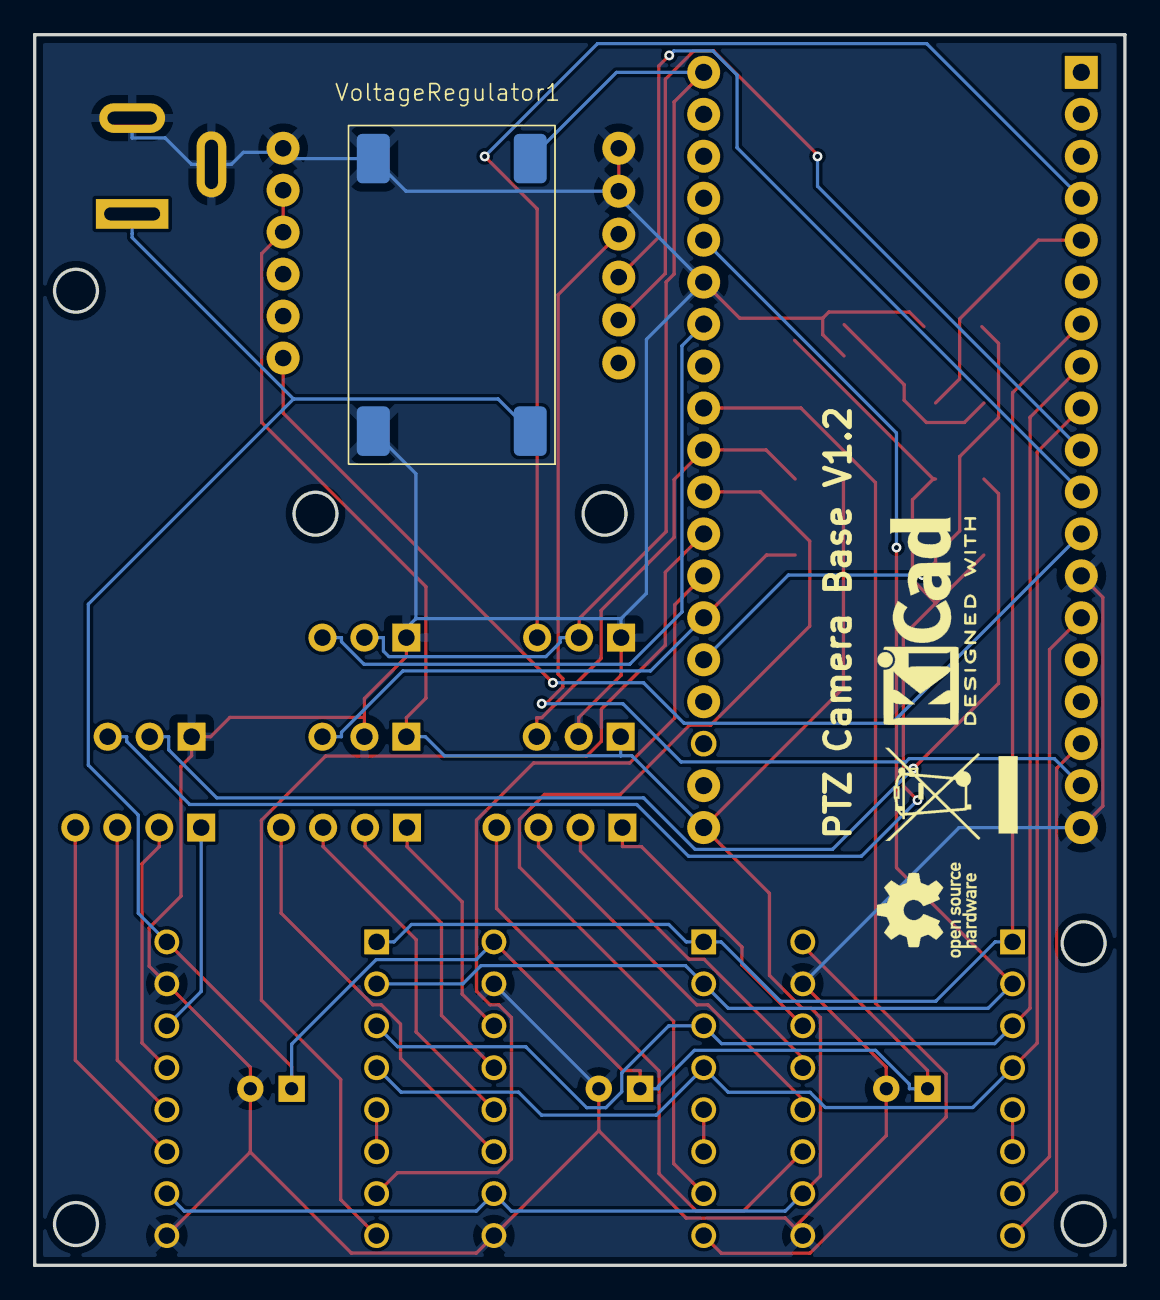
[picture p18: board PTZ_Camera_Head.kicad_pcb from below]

Board: 2 copper layers, 66.0 x 74.5 mm, 27 parts (3 on the bottom side), 42 nets.

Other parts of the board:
REF2: OSHW-Logo_5.7x6mm_SilkScreen
REF3: WEEE-Logo_5.6x8mm_SilkScreen

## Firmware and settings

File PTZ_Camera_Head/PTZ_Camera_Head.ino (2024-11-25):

#include <Arduino.h>
#include <SPI.h>
#include <Ethernet.h>
#include <AccelStepper.h>
#include <LANCControl.h>
#include <ESP32Servo.h>
#include <Preferences.h>

Preferences prefs;

Servo servo1;


#define dirPin1 22
#define stepPin1 21
#define dirPin2 27
#define stepPin2 25

#define servoPin 15


#define PAN_HOMING_OFFSET 2.5    // Adjust PanStepper offset in steps
#define TILT_HOMING_OFFSET -190  // Adjust TiltStepper offset in steps


unsigned long buttonPressStart[8] = { 0, 0, 0, 0, 0, 0, 0, 0 };  // Store the press start time for each button
const unsigned long holdDuration = 1000;
const unsigned long holdDurationShort = 500;


AccelStepper PanStepper(AccelStepper::DRIVER, stepPin1, dirPin1);
AccelStepper TiltStepper(AccelStepper::DRIVER, stepPin2, dirPin2);

// MAC address for the Ethernet shield
byte mac[] = { 0xDE, 0xAD, 0xBE, 0xEF, 0xFE, 0xED };

// Create a server that listens on port 8080
EthernetServer server(8080);

// Variables to receive from the client (all integers)
int variables[15];
int postionPan[8];
int postionTilt[8];

float moveSpeed = 1;
float panSpeedMulti = 1;
float moveSpeedMultiplier = 1;
float moveSpeedMultiplierOld = 1;
int knob1Old, knob1New, knob2Old, knob2New, knob3Old, knob3New;
float AccelerationPan = 0.14;
float AccelerationTilt = 0.14;
bool zooming = 0;



void movesteppers(void *prameters) {

  float delayedSpeedPan = 0;
  int speedPan = 0;
  int speedJoyPan = 0;
  int speedPan1 = 0;
  int lastSpeedPan = 0;
  bool panLeftLogic = 0;
  bool panRightLogic = 0;

  float delayedSpeedTilt = 0;
  int speedTilt = 0;
  int speedJoyTilt = 0;
  int speedTilt1 = 0;
  int lastSpeedTilt = 0;

  int notPressedButton2 = 0;
  int notPressedButton3 = 0;


  while (true) {
    AccelerationPan = (1900 * moveSpeed * moveSpeedMultiplier) / 35000;
    AccelerationTilt = (1900 * moveSpeed * moveSpeedMultiplier) / 35000;


    speedJoyPan = variables[10] - 1900;

    speedJoyPan = speedJoyPan * moveSpeed * moveSpeedMultiplier;


    //Left continuous pan
    if (variables[1] == 1 && panLeftLogic == 0 && notPressedButton2 == 0) {
      panLeftLogic = 1;
      panRightLogic = 0;
      notPressedButton2 = 1;
    }

    if (variables[1] == 0) {
      notPressedButton2 = 0;
    }

    if (panLeftLogic == 1) {
      if (((variables[10] - 1900) > 1200 || (variables[10] - 1900) < -1200 || variables[1] == 1) && notPressedButton2 == 0) {
        panLeftLogic = 0;
        speedJoyPan = 0;
        notPressedButton2 = 1;
      } else {
        speedJoyPan = 1000 * panSpeedMulti;
      }
    }


    //right continuous pan
    if (variables[2] == 1 && panRightLogic == 0 && notPressedButton3 == 0) {
      panRightLogic = 1;
      panLeftLogic = 0;
      notPressedButton3 = 1;
    }

    if (variables[2] == 0) {
      notPressedButton3 = 0;
    }

    if (panRightLogic == 1) {
      if (((variables[10] - 1900) > 1200 || (variables[10] - 1900) < -1200 || variables[2] == 1) && notPressedButton3 == 0) {
        panRightLogic = 0;
        speedJoyPan = 0;
        notPressedButton3 = 1;
      } else {
        speedJoyPan = -1000 * panSpeedMulti;
      }
    }




    if (speedJoyPan > delayedSpeedPan) {
      delayedSpeedPan = delayedSpeedPan + AccelerationPan;
    } else if (speedJoyPan < delayedSpeedPan) {
      delayedSpeedPan = delayedSpeedPan - AccelerationPan;
    } else {
    }

    speedPan = delayedSpeedPan;

    speedPan1 = speedPan;

    if (speedPan != 0) {
      speedPan = speedPan / 100;
      speedPan = speedPan * -speedPan;
      speedPan = speedPan * (speedPan1 / abs(speedPan1));
    }

    if (speedPan < 22 && speedPan > -22) {
      speedPan = 0;
    }

    if (PanStepper.currentPosition() < -2850) {
      if (speedPan < 0) {  // If motor is moving towards the negative limit, stop it
        speedPan = 0;
        delayedSpeedPan = 0;
      }
    }
    if (PanStepper.currentPosition() > 2850) {
      if (speedPan > 0) {  // If motor is moving towards the positive limit, stop it
        speedPan = 0;
        delayedSpeedPan = 0;
      }
    }

    if (speedPan != lastSpeedPan) {
      PanStepper.setSpeed(speedPan / 5);
      lastSpeedPan = speedPan;
    }

    if (speedPan != 0) {
      PanStepper.runSpeed();
    }

    speedJoyTilt = variables[11] - 1900;

    speedJoyTilt = speedJoyTilt * moveSpeed * moveSpeedMultiplier;

    if (speedJoyTilt > delayedSpeedTilt) {
      delayedSpeedTilt = delayedSpeedTilt + AccelerationTilt;
    } else if (speedJoyTilt < delayedSpeedTilt) {
      delayedSpeedTilt = delayedSpeedTilt - AccelerationTilt;
    } else {
    }

    speedTilt = delayedSpeedTilt;

    speedTilt1 = speedTilt;

    if (speedTilt != 0) {
      speedTilt = speedTilt / 100;
      speedTilt = speedTilt * -speedTilt;
      speedTilt = speedTilt * (speedTilt1 / abs(speedTilt1));
    }

    if (speedTilt < 20 && speedTilt > -20) {
      speedTilt = 0;
    }
    if (TiltStepper.currentPosition() < -1000) {
      if (speedTilt < 0) {  // If motor is moving towards the negative limit, stop it
        speedTilt = 0;
        delayedSpeedTilt = 0;
      }
    }
    if (TiltStepper.currentPosition() > 1000) {
      if (speedTilt > 0) {  // If motor is moving towards the positive limit, stop it
        speedTilt = 0;
        delayedSpeedTilt = 0;
      }
    }

    if (speedTilt != lastSpeedTilt) {
      TiltStepper.setSpeed(speedTilt / 16);
      lastSpeedTilt = speedTilt;
    }

    if (speedTilt != 0) {
      TiltStepper.runSpeed();
    }



    //Trigger Shutdown when button 4 is held for holdDuration Seconds
    unsigned long currentTime3 = millis();
    if (variables[3] == 1) {
      if (buttonPressStart[3] == 0) {
        buttonPressStart[3] = currentTime3;  // Record the time when the button was first pressed
      } else if (currentTime3 - buttonPressStart[3] >= holdDuration) {
        Serial.println("Button 4 held for holdDuration");
        ESP.restart();
        buttonPressStart[3] = 0;  // Reset to detect the next long press
      }
    } else if (currentTime3 - buttonPressStart[3] <= holdDurationShort) {  //if short press
      runToPostion(-2000, 900);

      // Save moveSpeed to non-volatile storage
      prefs.begin("my-app", false);
      prefs.putFloat("moveSpeed", moveSpeed);
      prefs.putFloat("panSpeedMulti", panSpeedMulti);
      prefs.end();
      panLeftLogic = 0;
      panRightLogic = 0;
      delayedSpeedPan = 0;
      Serial.println("Shutdown complete, moveSpeed and panSpeedMulti saved, and motors returned to home position.");
      panLeftLogic = 0;
      buttonPressStart[3] = 0;  // Reset to detect the next press
    } else {
      buttonPressStart[3] = 0;  // Reset if the button is released
    }


    // Button 5
    unsigned long currentTime4 = millis();
    if (variables[4] == 1) {
      if (buttonPressStart[4] == 0) {
        buttonPressStart[4] = currentTime4;                             // Record the time when the button was first pressed
      } else if (currentTime4 - buttonPressStart[4] >= holdDuration) {  //if long press
        Serial.println("Button 5 held for holdDuration");

        postionPan[4] = PanStepper.currentPosition();
        postionTilt[4] = TiltStepper.currentPosition();
        Serial.println("set postion button 5");

        // Save varibles to non-volatile storage
        prefs.begin("my-app", false);
        prefs.putInt("postionPan4", postionPan[4]);
        prefs.putInt("postionTilt4", postionTilt[4]);
        prefs.end();

        buttonPressStart[4] = 0;  // Reset to detect the next long press
      }
    } else if (currentTime4 - buttonPressStart[4] <= holdDurationShort) {  //if short press
      runToPostion(postionPan[4], postionTilt[4]);
      panLeftLogic = 0;
      panRightLogic = 0;
      delayedSpeedPan = 0;
      Serial.println("short press 5");
      buttonPressStart[4] = 0;  // Reset to detect the next press
    } else {
      buttonPressStart[4] = 0;  // Reset if the button is released
    }


    // Button 6
    unsigned long currentTime5 = millis();
    if (variables[5] == 1) {
      if (buttonPressStart[5] == 0) {
        buttonPressStart[5] = currentTime5;                             // Record the time when the button was first pressed
      } else if (currentTime5 - buttonPressStart[5] >= holdDuration) {  //if long press
        Serial.println("Button 6 held for holdDuration");

        postionPan[5] = PanStepper.currentPosition();
        postionTilt[5] = TiltStepper.currentPosition();
        Serial.println("set postion button 6");

        // Save varibles to non-volatile storage
        prefs.begin("my-app", false);
        prefs.putInt("postionPan5", postionPan[5]);
        prefs.putInt("postionTilt5", postionTilt[5]);
        prefs.end();

        buttonPressStart[5] = 0;  // Reset to detect the next long press
      }
    } else if (currentTime5 - buttonPressStart[5] <= holdDurationShort) {  //if short press
      runToPostion(postionPan[5], postionTilt[5]);
      panLeftLogic = 0;
      panRightLogic = 0;
      delayedSpeedPan = 0;
      Serial.println("short press 6");
      buttonPressStart[5] = 0;  // Reset to detect the next press
    } else {
      buttonPressStart[5] = 0;  // Reset if the button is released
    }


    // Button 7
    unsigned long currentTime6 = millis();
    if (variables[6] == 1) {
      if (buttonPressStart[6] == 0) {
        buttonPressStart[6] = currentTime6;                             // Record the time when the button was first pressed
      } else if (currentTime6 - buttonPressStart[6] >= holdDuration) {  //if long press
        Serial.println("Button 7 held for holdDuration");

        postionPan[6] = PanStepper.currentPosition();
        postionTilt[6] = TiltStepper.currentPosition();
        Serial.println("set postion button 7");

        // Save varibles to non-volatile storage
        prefs.begin("my-app", false);
        prefs.putInt("postionPan6", postionPan[6]);
        prefs.putInt("postionTilt6", postionTilt[6]);
        prefs.end();

        buttonPressStart[6] = 0;  // Reset to detect the next long press
      }
    } else if (currentTime6 - buttonPressStart[6] <= holdDurationShort) {  //if short press
      runToPostion(postionPan[6], postionTilt[6]);
      panLeftLogic = 0;
      panRightLogic = 0;
      delayedSpeedPan = 0;
      Serial.println("short press 7");
      buttonPressStart[6] = 0;  // Reset to detect the next press
    } else {
      buttonPressStart[6] = 0;  // Reset if the button is released
    }


    // Button 8
    unsigned long currentTime7 = millis();
    if (variables[7] == 1) {
      if (buttonPressStart[7] == 0) {
        buttonPressStart[7] = currentTime7;                             // Record the time when the button was first pressed
      } else if (currentTime7 - buttonPressStart[7] >= holdDuration) {  //if long press
        Serial.println("Button 8 held for holdDuration");

        postionPan[7] = PanStepper.currentPosition();
        postionTilt[7] = TiltStepper.currentPosition();
        Serial.println("set postion button 8");

        // Save varibles to non-volatile storage
        prefs.begin("my-app", false);

        prefs.putInt("postionPan7", postionPan[7]);
        prefs.putInt("postionTilt7", postionTilt[7]);
        prefs.end();

        buttonPressStart[7] = 0;  // Reset to detect the next long press
      }
    } else if (currentTime7 - buttonPressStart[7] <= holdDurationShort) {  //if short press
      runToPostion(postionPan[7], postionTilt[7]);
      panLeftLogic = 0;
      panRightLogic = 0;
      delayedSpeedPan = 0;
      Serial.println("short press 8");
      buttonPressStart[7] = 0;  // Reset to detect the next press
    } else {
      buttonPressStart[7] = 0;  // Reset if the button is released
    }
  }
}


void zoom(void *prameters) {
  int zoom = 0;
  while (true) {
    zoom = variables[9] - 1980;
    zoom = zoom / 20;
    if (zoom < 20 && zoom > -20) {
      zoom = 0;
      zooming == 0;
    } else {
      zooming == 1;
    }

    if (zoom > 0) {
      int zoomInSpeed = map(zoom, 0, 100, 0, 7);  // Map to zoom in states (0-7)
      ZoomIn(zoomInSpeed);                        // Call ZoomIn function
    } else if (zoom < 0) {
      int zoomOutSpeed = map(zoom, 0, -100, 0, 7);  // Map to zoom out states (0-7)
      ZoomOut(zoomOutSpeed);                        // Call ZoomOut function
    }
    vTaskDelay(5 / portTICK_PERIOD_MS);
  }
}


void controlServo(void *parameters) {
  vTaskDelay(150 / portTICK_PERIOD_MS);
  knob1Old = variables[12];
  while (true) {
    knob1New = variables[12];

    if (knob1New >= knob1Old + 1) {
      for (int i = 0; i < 250; i++) {
        servo1.write(110);
        vTaskDelay(1.5 / portTICK_PERIOD_MS);
      }
    } else if (knob1New <= knob1Old - 1) {
      for (int i = 0; i < 250; i++) {
        servo1.write(70);
        vTaskDelay(1.5 / portTICK_PERIOD_MS);
      }
    } else {
      servo1.write(90);
    }
    knob1Old = knob1New;
    vTaskDelay(10 / portTICK_PERIOD_MS);
  }
}



void setup() {
  Serial.begin(115200);

  delay(500);

  setupLANC();

  // Allow allocation of all timers for ESP32Servo
  ESP32PWM::allocateTimer(0);
  ESP32PWM::allocateTimer(1);
  ESP32PWM::allocateTimer(2);
  ESP32PWM::allocateTimer(3);

  // Attach the servo
  servo1.setPeriodHertz(50);            // Standard 50 Hz servo
  servo1.attach(servoPin, 1000, 2000);  // Attach the servo to the pin with min/max pulse widths


  delay(500);
  Serial.println("Initializing Ethernet...");

  Ethernet.init(5);  // Set the CS pin (5 for W5500)

  // Start Ethernet with DHCP
  if (Ethernet.begin(mac) == 0) {
    Serial.println("Failed to configure Ethernet using DHCP");
    while (true)
      ;  // Halt execution if DHCP fails
  } else {
    Serial.println("DHCP configured successfully");
  }
  delay(2000);

  // Print local IP
  Serial.println("Server is at IP: ");
  Serial.println(Ethernet.localIP());

  // Start listening for clients
  server.begin();

  pinMode(4, OUTPUT);
  pinMode(13, OUTPUT);
  pinMode(16, OUTPUT);

  digitalWrite(4, LOW);
  digitalWrite(13, LOW);
  digitalWrite(16, LOW);

  PanStepper.setMaxSpeed(2000);
  TiltStepper.setMaxSpeed(2000);
  PanStepper.setAcceleration(1000);
  TiltStepper.setAcceleration(1000);

  // Recalling Values from memory
  prefs.begin("my-app", false);

  // Load the saved moveSpeed value if it exists
  if (prefs.isKey("moveSpeed")) {
    moveSpeed = prefs.getFloat("moveSpeed", 2.0);
    Serial.println("Loaded moveSpeed: ");
    Serial.println(moveSpeed);
  }

  if (prefs.isKey("panSpeedMulti")) {
    panSpeedMulti = prefs.getFloat("panSpeedMulti", 2.0);
    Serial.println("Loaded panSpeedMulti: ");
    Serial.println(panSpeedMulti);
  }

  if (prefs.isKey("postionTilt4")) {
    postionTilt[4] = prefs.getInt("postionTilt4", 2.0);
    Serial.println("Loaded postionTilt4: ");
    Serial.println(postionTilt[4]);
  }
  if (prefs.isKey("postionPan4")) {
    postionPan[4] = prefs.getInt("postionPan4", 2.0);
    Serial.println("Loaded postionPan4: ");
    Serial.println(postionPan[4]);
  }

  if (prefs.isKey("postionTilt5")) {
    postionTilt[5] = prefs.getInt("postionTilt5", 2.0);
    Serial.println("Loaded postionTilt5: ");
    Serial.println(postionTilt[5]);
  }
  if (prefs.isKey("postionPan5")) {
    postionPan[5] = prefs.getInt("postionPan5", 2.0);
    Serial.println("Loaded postionPan5: ");
    Serial.println(postionPan[5]);
  }

  if (prefs.isKey("postionTilt6")) {
    postionTilt[6] = prefs.getInt("postionTilt6", 2.0);
    Serial.println("Loaded postionTilt6: ");
    Serial.println(postionTilt[6]);
  }
  if (prefs.isKey("postionPan6")) {
    postionPan[6] = prefs.getInt("postionPan6", 2.0);
    Serial.println("Loaded postionPan6: ");
    Serial.println(postionPan[6]);
  }

  if (prefs.isKey("postionTilt7")) {
    postionTilt[7] = prefs.getInt("postionTilt7", 2.0);
    Serial.println("Loaded postionTilt7: ");
    Serial.println(postionTilt[7]);
  }
  if (prefs.isKey("postionPan7")) {
    postionPan[7] = prefs.getInt("postionPan7", 2.0);
    Serial.println("Loaded postionPan7: ");
    Serial.println(postionPan[7]);
  }
  // End of recalling moveSpeed from memory

  prefs.end();


  // Homing PanStepper
  pinMode(26, INPUT);
  PanStepper.setSpeed(1000);
  int counter = 0;
  while (digitalRead(26) == 1) {
    PanStepper.runSpeed();
    delay(1.5);
    counter++;
    if (counter >= 3500) {
      break;  // Exit loop after 3500 iterations
    }
  }
  PanStepper.setSpeed(-1000);
  while (digitalRead(26) == 1) {
    PanStepper.runSpeed();
    delay(1.5);
  }

  PanStepper.move(-750);  // Move 500 steps forward
  PanStepper.runToPosition();

  PanStepper.setSpeed(250);
  while (digitalRead(26) == 1) {
    PanStepper.runSpeed();
    delay(1.5);
  }

  // Move PanStepper by offset after homing
  PanStepper.move(PAN_HOMING_OFFSET);
  PanStepper.runToPosition();  // Ensure it reaches the offset position
  Serial.println("PanStepper homing done");

  // Homing TiltStepper
  pinMode(35, INPUT);
  TiltStepper.setSpeed(-1000);
  counter = 0;
  while (digitalRead(35) == 1) {
    TiltStepper.runSpeed();
    delay(1);
    counter++;
    if (counter >= 2500) {
      break;  // Exit loop after 2500 iterations
    }
  }
  TiltStepper.setSpeed(1000);
  while (digitalRead(35) == 1) {
    TiltStepper.runSpeed();
    delay(1.5);
  }

  TiltStepper.move(500);  // Move 500 steps forward
  TiltStepper.runToPosition();

  TiltStepper.setSpeed(-250);
  while (digitalRead(35) == 1) {
    TiltStepper.runSpeed();
    delay(1.5);
  }

  TiltStepper.move(105);
  TiltStepper.runToPosition();

  // Move TiltStepper by offset after homing
  TiltStepper.move(TILT_HOMING_OFFSET);
  TiltStepper.runToPosition();  // Ensure it reaches the offset position
  Serial.println("TiltStepper homing done");

  PanStepper.setCurrentPosition(0);
  TiltStepper.setCurrentPosition(0);

  xTaskCreate(
    movesteppers,     // Funcction name
    "Move Steppers",  // Task Name
    10000,            // stack size
    NULL,             // task parameters
    1,                // task priority
    NULL              // task handel
  );

  xTaskCreate(
    zoom,    // Funcction name
    "Zoom",  // Task Name
    4000,    // stack size
    NULL,    // task parameters
    1,       // task priority
    NULL     // task handel
  );

  xTaskCreate(
    controlServo,     // Function to run the task
    "Control Servo",  // Task name
    4000,             // Stack size
    NULL,             // Task parameters
    1,                // Task priority
    NULL              // Task handle
  );
}


String readStringUntil(EthernetClient &client, char terminator) {
  String value = "";
  char c;
  while (client.available()) {
    c = client.read();
    if (c == terminator) break;
    value += c;
  }
  return value;
}

int readIntVariable(EthernetClient &client) {
  String value = "";
  char c;
  while (client.available()) {
    c = client.read();
    if (c == '\n') break;  // Stop reading at newline
    value += c;
  }
  return value.toInt();
}

void printReceivedVariables() {
  for (int i = 0; i < 15; i++) {
    Serial.println("Variable ");
    Serial.println(i + 1);
    Serial.println(": ");
    Serial.println(variables[i]);
  }
}

void runToPostion(int PanPostion, int TiltPostion) {
  // Action for button 2 - Move both motors to target positions
  PanStepper.moveTo(PanPostion);
  TiltStepper.moveTo(TiltPostion);

  // Calculate the distances to travel
  long panDistance = PanStepper.distanceToGo();
  long tiltDistance = TiltStepper.distanceToGo();

  // Calculate the speed ratio to synchronize arrival times
  float maxDistance = max(abs(panDistance), abs(tiltDistance));
  float panSpeed = 500.0 * (abs(panDistance) / maxDistance);
  float tiltSpeed = 500.0 * (abs(tiltDistance) / maxDistance);

  // Set the speeds with appropriate direction
  PanStepper.setSpeed(panSpeed * (panDistance < 0 ? -1 : 1));
  TiltStepper.setSpeed(tiltSpeed * (tiltDistance < 0 ? -1 : 1));

  // Run both motors until they reach their target positions
  while (PanStepper.distanceToGo() != 0 || TiltStepper.distanceToGo() != 0) {
    PanStepper.run();
    TiltStepper.run();
  }
}

unsigned long lastCommunicationTime = 0;
const unsigned long timeoutDuration = 200;  // 5 seconds timeout

void resetNonEncoderVariables() {
  // Reset button and joystick variables
  for (int i = 0; i < 8; i++) {
    variables[i] = 0;  // Reset buttons to 0
  }
  for (int i = 8; i < 12; i++) {
    variables[i] = 1900;  // Reset joysticks to 1900
  }
}








String dataBuffer = "";  // Buffer to accumulate incoming data
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
void loop() {
  receive_variables();
  vTaskDelay(150 / portTICK_PERIOD_MS);
  knob2Old = variables[13];
  while (true) {
    receive_variables();
    connectionTimeout();
    adjustSpeed();
    vTaskDelay(5 / portTICK_PERIOD_MS);
  }
}

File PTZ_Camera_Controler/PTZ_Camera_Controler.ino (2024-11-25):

#include <Arduino.h>
#include <Adafruit_NeoPixel.h>
#include <ESP_Knob.h>
#include <SPI.h>
#include <Ethernet.h>
#include <PS4Controller.h>


#define LedPin 16
#define Buttonpin1 4
#define Buttonpin2 13
#define Buttonpin3 14
#define Buttonpin4 36
#define Buttonpin5 39
#define Buttonpin6 15
#define Buttonpin7 2
#define Buttonpin8 12
#define Joypin1x 33
#define Joypin1y 32
#define Joypin2x 35
#define Joypin2y 34
#define RE_1_1 17

#define RE_1_2 21
#define RE_2_1 22
#define RE_2_2 25
#define RE_3_1 26
#define RE_3_2 27

#define NUM_LEDS 7

//use the SixaxisPairTool to fiugure the Mac Address of the PS4 and put it in the PS4.begin in the startup

// Server IP and port configuration
IPAddress server(10, 69, 2, 122);  //change the Server IP Address to the cameras IP Address    10, 69, 2, 122
const int port = 8080;

// MAC address for the Ethernet shield
byte mac[] = { 0xDE, 0xAD, 0xBE, 0xEF, 0xFE, 0xEE };

EthernetClient client;



int variables[15];


unsigned long buttonPressStart[8] = { 0, 0, 0, 0, 0, 0, 0, 0 };  // Store the press start time for each button
const unsigned long holdDuration = 1000;
const unsigned long holdDurationShort = 500;


Adafruit_NeoPixel strip = Adafruit_NeoPixel(NUM_LEDS, LedPin, NEO_GRB + NEO_KHZ800);


ESP_Knob knob1(RE_1_1, RE_1_2);
ESP_Knob knob2(RE_2_1, RE_2_2);
ESP_Knob knob3(RE_3_1, RE_3_2);

int knob1Count = 0;
int knob2Count = 0;
int knob3Count = 0;
bool R1Bool = 1;

int knob1Old, knob1New, knob2Old, knob2New, knob3Old, knob3New;


void setColorAll(uint32_t color) {
  for (int i = 0; i < NUM_LEDS; i++) {
    strip.setPixelColor(i, color);  // Set the color for each pixel
  }
  strip.show();  // Update the strip with the new color
}


void lightsForKnobs(void *prameters) {
  while (true) {
    knob1New = knob1Count;

    if (knob1New == knob1Old + 1) {
      strip.setPixelColor(0, strip.Color(0, 0, 255));
      strip.show();
    }

    if (knob1New == knob1Old - 1) {
      strip.setPixelColor(0, strip.Color(0, 0, 255));
      strip.show();
    }
    knob1Old = knob1New;


    knob2New = knob2Count;

    if (knob2New == knob2Old + 1) {
      strip.setPixelColor(1, strip.Color(0, 0, 255));
      strip.show();
    }

    if (knob2New == knob2Old - 1) {
      strip.setPixelColor(1, strip.Color(0, 0, 255));
      strip.show();
    }
    knob2Old = knob2New;


    knob3New = knob3Count;

    if (knob3New == knob3Old + 1) {
      strip.setPixelColor(2, strip.Color(0, 0, 255));
      strip.show();
    }

    if (knob3New == knob3Old - 1) {
      strip.setPixelColor(2, strip.Color(0, 0, 255));
      strip.show();
    }
    knob3Old = knob3New;
    vTaskDelay(1.5 / portTICK_PERIOD_MS);
  }
}


void lightsForButtons(void *prameters) {
  while (true) {
    // Button 1
    if (digitalRead(Buttonpin1) == 1) {
      strip.setPixelColor(3, strip.Color(0, 0, 255));
      strip.show();
    }

    // Button 2
    unsigned long currentTime1 = millis();
    if (digitalRead(Buttonpin2) == 1) {
      if (buttonPressStart[1] == 0) {
        buttonPressStart[1] = currentTime1;                             // Record the time when the button was first pressed
      } else if (currentTime1 - buttonPressStart[1] >= holdDuration) {  //if long press
                                                                        //Action if long
        buttonPressStart[1] = 0;                                        // Reset to detect the next long press
      }
      vTaskDelay(200 / portTICK_PERIOD_MS);
    } else if (currentTime1 - buttonPressStart[1] <= holdDurationShort) {  //if short press
      for (int i = 0; i < 100; i++) {
        strip.setPixelColor(4, strip.Color(0, 0, 255));
        strip.show();
        vTaskDelay(2 / portTICK_PERIOD_MS);
      }
      //Serial.println("short press 2");
      buttonPressStart[1] = 0;  // Reset to detect the next press
    } else {
      buttonPressStart[1] = 0;  // Reset if the button is released
    }


    // Button 3
    unsigned long currentTime2 = millis();
    if (digitalRead(Buttonpin3) == 1) {
      if (buttonPressStart[2] == 0) {
        buttonPressStart[2] = currentTime2;                             // Record the time when the button was first pressed
      } else if (currentTime2 - buttonPressStart[2] >= holdDuration) {  //if long press
                                                                        //Action if long
        buttonPressStart[2] = 0;                                        // Reset to detect the next long press
      }
      vTaskDelay(200 / portTICK_PERIOD_MS);
    } else if (currentTime2 - buttonPressStart[2] <= holdDurationShort) {  //if short press
      for (int i = 0; i < 100; i++) {
        strip.setPixelColor(5, strip.Color(0, 0, 255));
        strip.show();
        vTaskDelay(2 / portTICK_PERIOD_MS);
      }
      //Serial.println("short press 3");
    } else {
      buttonPressStart[2] = 0;  // Reset if the button is released
    }


    // Button 4
    unsigned long currentTime3 = millis();
    if (digitalRead(Buttonpin4) == 1) {
      if (buttonPressStart[3] == 0) {
        buttonPressStart[3] = currentTime3;                             // Record the time when the button was first pressed
      } else if (currentTime3 - buttonPressStart[3] >= holdDuration) {  //if long press
                                                                        //Serial.println("Button 5 held for holdDuration");
        for (int i = 0; i < 100; i++) {
          strip.setPixelColor(6, strip.Color(255, 0, 0));
          strip.show();
          vTaskDelay(2 / portTICK_PERIOD_MS);
        }
        buttonPressStart[3] = 0;  // Reset to detect the next long press
      }
      vTaskDelay(200 / portTICK_PERIOD_MS);
    } else if (currentTime3 - buttonPressStart[3] <= holdDurationShort) {  //if short press

      for (int i = 0; i < 100; i++) {
        strip.setPixelColor(6, strip.Color(0, 0, 255));
        strip.show();
        vTaskDelay(2 / portTICK_PERIOD_MS);
      }

      //Serial.println("short press 5");
      buttonPressStart[3] = 0;  // Reset to detect the next press
    } else {
      buttonPressStart[3] = 0;  // Reset if the button is released
    }
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

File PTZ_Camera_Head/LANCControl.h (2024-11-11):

#ifndef LANC_CONTROL_H
#define LANC_CONTROL_H

int PinLANC = 34;  // 5V limited input signal from LANC data
int PinCMD = 2;   // Command to send to LANC
byte typeCam = B00101000;
byte typeVTR = B00011000;
int bitDuration = 100;  // Writing to the digital port takes about 8 microseconds so only 96 microseconds are left

// Function prototypes
void ZoomOut(int Wide);
void ZoomIn(int In);
void Focus(int direction);
void sendCMD(unsigned char cmd1, unsigned char cmd2);

// LANC initialization
void setupLANC() {
    pinMode(PinLANC, INPUT);
    pinMode(PinCMD, OUTPUT);
}

// Zoom out function
void ZoomOut(int Wide) {
    switch (Wide) {
        case 0: sendCMD(typeCam, B00010000); break;
        case 1: sendCMD(typeCam, B00010010); break;
        case 2: sendCMD(typeCam, B00010100); break;
        case 3: sendCMD(typeCam, B00010110); break;
        case 4: sendCMD(typeCam, B00011000); break;
        case 5: sendCMD(typeCam, B00011010); break;
        case 6: sendCMD(typeCam, B00011100); break;
        case 7: sendCMD(typeCam, B00011110); break;
    }
}

// Zoom in function
void ZoomIn(int In) {
    switch (In) {
        case 0: sendCMD(typeCam, B00000000); break;
        case 1: sendCMD(typeCam, B00000010); break;
        case 2: sendCMD(typeCam, B00000100); break;
        case 3: sendCMD(typeCam, B00000110); break;
        case 4: sendCMD(typeCam, B00001000); break;
        case 5: sendCMD(typeCam, B00001010); break;
        case 6: sendCMD(typeCam, B00001100); break;
        case 7: sendCMD(typeCam, B00001110); break;
    }
}

// Focus function
void Focus(int direction) {
    switch (direction) {
        case 0: sendCMD(typeCam, 0x45); break;  // Focus Far
        case 1: sendCMD(typeCam, 0x47); break;  // Focus Near
    }
}

// Send LANC command
void sendCMD(unsigned char cmd1, unsigned char cmd2) {
    for (int cmdRepeatCount = 0; cmdRepeatCount < 5; cmdRepeatCount++) {  // Repeat 5 times to ensure the camera accepts the command
        while (pulseIn(PinLANC, HIGH) < 5000) {
            // Wait for a new data packet start
        }
        delayMicroseconds(bitDuration);  // Wait START bit duration

        for (int i = 0; i < 8; i++) {
            digitalWrite(PinCMD, (cmd1 & (1 << i)) ? HIGH : LOW);
            delayMicroseconds(bitDuration);
        }

        digitalWrite(PinCMD, LOW);  // Set LANC line back to +5V
        delayMicroseconds(10);  // Ensure we are in the stop bit before byte 1

        while (digitalRead(PinLANC)) {
            // Wait for the stop bit to finish
        }
        
        delayMicroseconds(bitDuration);  // Wait START bit duration for Byte 1

        for (int i = 0; i < 8; i++) {
            digitalWrite(PinCMD, (cmd2 & (1 << i)) ? HIGH : LOW);
            delayMicroseconds(bitDuration);
        }

        digitalWrite(PinCMD, LOW);  // Set LANC line back to +5V
    }
}

#endif

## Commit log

2024-11-11 Uploaded Pictures of PCB Schematics
    [Base.stl, Left Stopper.stl, Right Stopper.stl]
2024-11-25 Fix preset not working and inverted ps4 joysticks
    [PTZ_Camera_Controler.ino, PTZ_Camera_Head.ino]
